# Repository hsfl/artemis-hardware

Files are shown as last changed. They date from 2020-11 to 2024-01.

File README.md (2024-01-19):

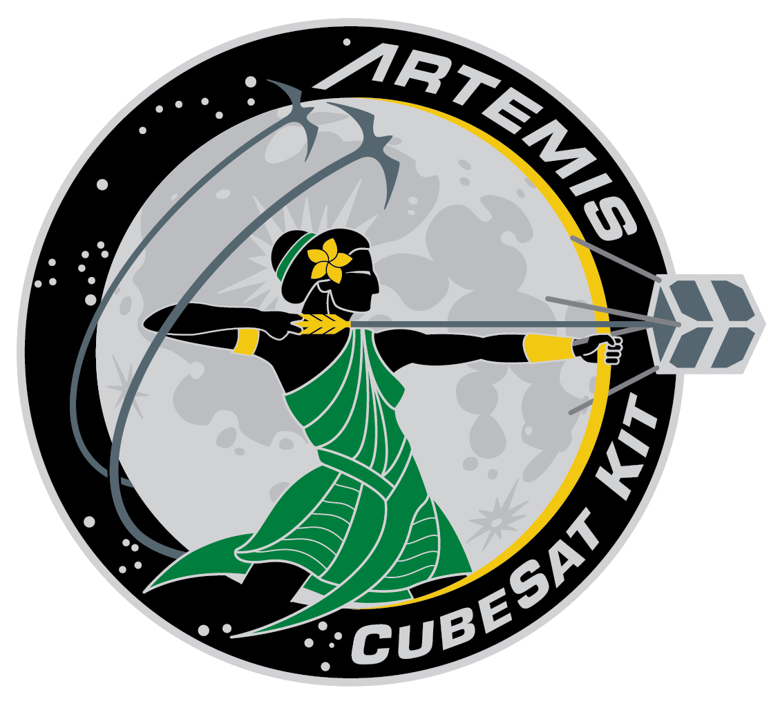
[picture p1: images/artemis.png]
Artemis
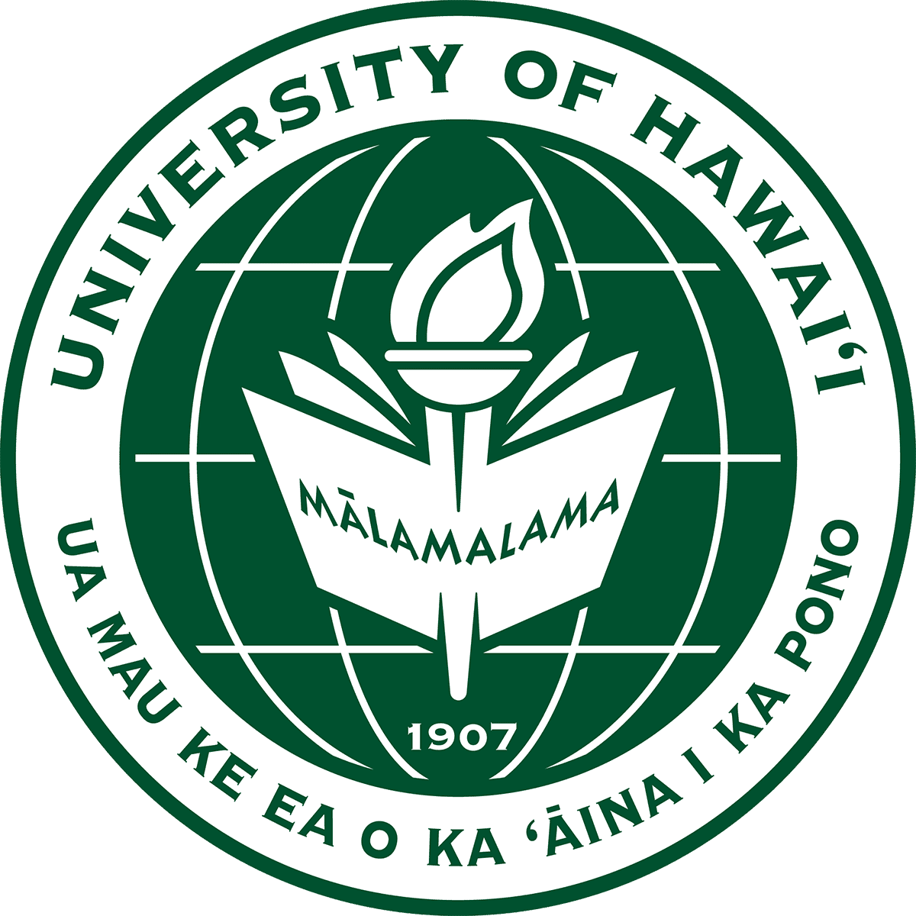
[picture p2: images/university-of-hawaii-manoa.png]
University of Hawaii Manoa
  <br>

# Artemis Cubesat Kit Hardware

This repository contains CAD models, Eagle designs, and thermal analysis for the Artemis Cubesat Kit V1.

For documentation and tutorials, visit our [project website](https://sites.google.com/hawaii.edu/artemiscubesatkit).

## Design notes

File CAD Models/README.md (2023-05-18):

Artemis University of Hawaii Manoa <br>

# Artemis Cubesat Kit Hardware

Within this folder are the solidworks files for the Artemis CubeSat.

Models were made using SolidWorks 2020, be sure to have SolidWorks 2020 or up to open the files.
If you do not have access to Solidworks, you can use OnShape to view the model as a zip file.

Due to file size limit, only the structure was uploaded.

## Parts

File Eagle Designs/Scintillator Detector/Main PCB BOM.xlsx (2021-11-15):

Part | Value | Device
C1 | 10uF | CAP0805
C2, C9 | 0.1uF | CAP0805
C3 | 10pF | CAP0805
C4 | 20nF | CAP0805
C5, C8 | 1uF | CAP0805
C6 | 22pF | CAP0805
C7 | 0.47uF | CAP0805
D1, D2 | RBR1VWM40ATR | RBR1VWM40ATR
J1, J2 | 503763-0591 | 503763-0591
L1 | 47uH | LQH32CN470K53L
L2 | BK2125LM252-T | BK2125LM252-T
R1 | 1k | RESISTOR0805-RES
R2 | 249 | RESISTOR0805-RES
R3, R4, R10, R13 | 10k | RESISTOR0805-RES
R5, R6 | 100k | RESISTOR0805-RES
R7, R9 | 0 | RESISTOR0805-RES
R8 | 24.9k | RESISTOR0805-RES
R11 | 226k | RESISTOR0805-RES
R12 | 45.3k | RESISTOR0805-RES
U1 | LT1807IS8PBF | LT1807IS8PBF
U2 | LT3461AES6TRMPBF | LT3461AES6TRMPBF
U3 | TMP36FSZ | TMP36FSZ

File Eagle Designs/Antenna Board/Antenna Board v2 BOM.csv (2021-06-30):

Part | Value | Device | Package | Description | AUTOMOTIVE | BUILT_BY | CENTROID_NOT_SPECIFIED | CONN_GENDER | CONN_ORIENTATION | CONTACT_MATERIAL | COPYRIGHT | CURRENT_RATING | DATASHEET | DEVICE_CLASS_L1 | DEVICE_CLASS_L2 | DEVICE_CLASS_L3 | DIGIKEY_DESCRIPTION | DIGIKEY_PART_NUMBER | FOOTPRINT_URL | FOOTPRINT_VARIANT_NAME_0 | HEIGHT | LEAD_FREE | MANUFACTURER_PART_NUMBER | MF | MFG_PACKAGE_IDENT | MFG_PACKAGE_IDENT_DATE | MFG_PACKAGE_IDENT_REV | MOUSER_PART_NUMBER | MPN | NUMBER_OF_CONTACTS | NUMBER_OF_ROWS | PACKAGE | PITCH | PREFIX | ROHS | SOURCELIBRARY | TEMPERATURE_RANGE_HIGH | TEMPERATURE_RANGE_LOW | VENDOR | VERIFICATION_VERSION | VOLTAGE_RATING
J1 | 503763-0591 | 503763-0591 | CONN_5037630591_MOL |  |  | EMA_Cory |  |  |  |  | Copyright (C) 2018 Accelerated Designs. All rights reserved |  | https://www.molex.com/pdm_docs/sd/5037630591_sd.pdf |  |  |  |  |  |  |  |  |  | 503763-0591 |  |  |  |  |  |  |  |  |  |  |  |  | Add_to_database_2020-12-14 |  |  | Molex Connector Corporation
J2 | MOLEX_503763-0491MOLEX_503763-0491_0_0 | MOLEX_503763-0491MOLEX_503763-0491_0_0 | MOLEX_503763-0491_0 | Wire-To-Board Connector, Pico-Lock 503763 Series, Surface Mount, Header, 4 Contacts, 1 mm | No |  | No | Male | Right Angle | Gold,Nickel |  | 1.5A | https://www.molex.com/webdocs/datasheets/pdf/en-us/5037630491_PCB_HEADERS.pdf | Connectors | Headers and Wire Housings | unset | CONN HEADER 1MM R/A 4CKT | WM10655CT-ND | https://www.molex.com/pdm_docs/sd/5037630491_sd.pdf | Recommended_Land_Pattern | 1.7mm | Yes |  | Molex | 503763-0491 | 0 | 0 | 538-503763-0491 | 503763-0491 | 4 | 1 | HDR4 | 1mm | J | Yes |  | +105°C | -40°C |  | 0.0.0.1 | 150V
J3 | MOLEX_503763-0491MOLEX_503763-0491_0_0 | MOLEX_503763-0491MOLEX_503763-0491_0_0 | MOLEX_503763-0491_0 | Wire-To-Board Connector, Pico-Lock 503763 Series, Surface Mount, Header, 4 Contacts, 1 mm | No |  | No | Male | Right Angle | Gold,Nickel |  | 1.5A | https://www.molex.com/webdocs/datasheets/pdf/en-us/5037630491_PCB_HEADERS.pdf | Connectors | Headers and Wire Housings | unset | CONN HEADER 1MM R/A 4CKT | WM10655CT-ND | https://www.molex.com/pdm_docs/sd/5037630491_sd.pdf | Recommended_Land_Pattern | 1.7mm | Yes |  | Molex | 503763-0491 | 0 | 0 | 538-503763-0491 | 503763-0491 | 4 | 1 | HDR4 | 1mm | J | Yes |  | +105°C | -40°C |  | 0.0.0.1 | 150V
J4 | MOLEX_503763-0291MOLEX_503763-0291_0_0 | MOLEX_503763-0291MOLEX_503763-0291_0_0 | MOLEX_503763-0291_0 | 2 Positions Header Connector 0.039 (1.00mm) Surface Mount, Right Angle Gold" |  |  | No |  |  |  |  |  | http://www.molex.com/pdm_docs/sd/5037630291_sd.pdf |  |  |  | CONN HEADER 1MM R/A 2CKT | WM10654CT-ND |  |  |  | yes |  | Molex |  |  |  | 538-503763-0291 | 503763-0291 |  |  | HDR02 |  | J | yes |  | +105°C | -40°C
J5 | 503763-0591 | 503763-0591 | CONN_5037630591_MOL |  |  | EMA_Cory |  |  |  |  | Copyright (C) 2018 Accelerated Designs. All rights reserved |  | https://www.molex.com/pdm_docs/sd/5037630591_sd.pdf |  |  |  |  |  |  |  |  |  | 503763-0591 |  |  |  |  |  |  |  |  |  |  |  |  | Add_to_database_2020-12-14 |  |  | Molex Connector Corporation
J6 | MOLEX_503763-0491MOLEX_503763-0491_0_0 | MOLEX_503763-0491MOLEX_503763-0491_0_0 | MOLEX_503763-0491_0 | Wire-To-Board Connector, Pico-Lock 503763 Series, Surface Mount, Header, 4 Contacts, 1 mm | No |  | No | Male | Right Angle | Gold,Nickel |  | 1.5A | https://www.molex.com/webdocs/datasheets/pdf/en-us/5037630491_PCB_HEADERS.pdf | Connectors | Headers and Wire Housings | unset | CONN HEADER 1MM R/A 4CKT | WM10655CT-ND | https://www.molex.com/pdm_docs/sd/5037630491_sd.pdf | Recommended_Land_Pattern | 1.7mm | Yes |  | Molex | 503763-0491 | 0 | 0 | 538-503763-0491 | 503763-0491 | 4 | 1 | HDR4 | 1mm | J | Yes |  | +105°C | -40°C |  | 0.0.0.1 | 150V
J7 | MOLEX_503763-0491MOLEX_503763-0491_0_0 | MOLEX_503763-0491MOLEX_503763-0491_0_0 | MOLEX_503763-0491_0 | Wire-To-Board Connector, Pico-Lock 503763 Series, Surface Mount, Header, 4 Contacts, 1 mm | No |  | No | Male | Right Angle | Gold,Nickel |  | 1.5A | https://www.molex.com/webdocs/datasheets/pdf/en-us/5037630491_PCB_HEADERS.pdf | Connectors | Headers and Wire Housings | unset | CONN HEADER 1MM R/A 4CKT | WM10655CT-ND | https://www.molex.com/pdm_docs/sd/5037630491_sd.pdf | Recommended_Land_Pattern | 1.7mm | Yes |  | Molex | 503763-0491 | 0 | 0 | 538-503763-0491 | 503763-0491 | 4 | 1 | HDR4 | 1mm | J | Yes |  | +105°C | -40°C |  | 0.0.0.1 | 150V
J8 | MOLEX_503763-0291MOLEX_503763-0291_0_0 | MOLEX_503763-0291MOLEX_503763-0291_0_0 | MOLEX_503763-0291_0 | 2 Positions Header Connector 0.039 (1.00mm) Surface Mount, Right Angle Gold" |  |  | No |  |  |  |  |  | http://www.molex.com/pdm_docs/sd/5037630291_sd.pdf |  |  |  | CONN HEADER 1MM R/A 2CKT | WM10654CT-ND |  |  |  | yes |  | Molex |  |  |  | 538-503763-0291 | 503763-0291 |  |  | HDR02 |  | J | yes |  | +105°C | -40°C
J9 | MOLEX_503763-0291MOLEX_503763-0291_0_0 | MOLEX_503763-0291MOLEX_503763-0291_0_0 | MOLEX_503763-0291_0 | 2 Positions Header Connector 0.039 (1.00mm) Surface Mount, Right Angle Gold" |  |  | No |  |  |  |  |  | http://www.molex.com/pdm_docs/sd/5037630291_sd.pdf |  |  |  | CONN HEADER 1MM R/A 2CKT | WM10654CT-ND |  |  |  | yes |  | Molex |  |  |  | 538-503763-0291 | 503763-0291 |  |  | HDR02 |  | J | yes |  | +105°C | -40°C
J10 | U.FL-R-SMT-1(01) | U.FL-R-SMT-1(01) | CONN_-SMT-1(01) |  |  | EMA_Matt |  |  |  |  | Copyright (C) 2018 Accelerated Designs. All rights reserved |  |  |  |  |  |  |  |  |  |  |  | U.FL-R-SMT-1(01) |  |  |  |  |  |  |  |  |  |  |  |  | Hirose_12_20_2019 |  |  | Hirose
J11 | U.FL-R-SMT-1(01) | U.FL-R-SMT-1(01) | CONN_-SMT-1(01) |  |  | EMA_Matt |  |  |  |  | Copyright (C) 2018 Accelerated Designs. All rights reserved |  |  |  |  |  |  |  |  |  |  |  | U.FL-R-SMT-1(01) |  |  |  |  |  |  |  |  |  |  |  |  | Hirose_12_20_2019 |  |  | Hirose
J12 | U.FL-R-SMT-1(01) | U.FL-R-SMT-1(01) | CONN_-SMT-1(01) |  |  | EMA_Matt |  |  |  |  | Copyright (C) 2018 Accelerated Designs. All rights reserved |  |  |  |  |  |  |  |  |  |  |  | U.FL-R-SMT-1(01) |  |  |  |  |  |  |  |  |  |  |  |  | Hirose_12_20_2019 |  |  | Hirose
U$2 | ANTENNA_PAD | ANTENNA_PAD | ANTENNA_PAD
U$3 | BURNWIRE | BURNWIRE | BURNWIRE

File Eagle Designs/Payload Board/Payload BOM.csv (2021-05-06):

Part | Value | Device | Package | Description | ARROW_PART_NUMBER | ARROW_PRICE-STOCK | AUTOMOTIVE | AVAILABILITY | BUILT_BY | CENTROID_NOT_SPECIFIED | CONN_GENDER | CONN_ORIENTATION | CONTACT_MATERIAL | COPYRIGHT | CURRENT_RATING | DATASHEET | DESCRIPTION | DEVICE_CLASS_L1 | DEVICE_CLASS_L2 | DEVICE_CLASS_L3 | DIGIKEY_DESCRIPTION | DIGIKEY_PART_NUMBER | FOOTPRINT_URL | FOOTPRINT_VARIANT_NAME_0 | HEIGHT | LEAD_FREE | MANUFACTURER_NAME | MANUFACTURER_PART_NUMBER | MF | MFG_PACKAGE_IDENT | MFG_PACKAGE_IDENT_DATE | MFG_PACKAGE_IDENT_REV | MOUSER_PART_NUMBER | MOUSER_PRICE-STOCK | MP | MPN | NUMBER_OF_CONTACTS | NUMBER_OF_ROWS | OC_FARNELL | OC_NEWARK | PACKAGE | PITCH | PREFIX | PRICE | PURCHASE-URL | ROHS | SOURCELIBRARY | TEMPERATURE_RANGE_HIGH | TEMPERATURE_RANGE_LOW | VENDOR | VERIFICATION_VERSION | VOLTAGE_RATING
C1 | 22uF | CAP0805 | 0805 | Capacitor
C2 | 22uF | CAP0805 | 0805 | Capacitor
C3 | 0.1uF | CAP0805 | 0805 | Capacitor
C4 | 1uF | CAP0805 | 0805 | Capacitor
C5 | 0.47uF | CAP0805 | 0805 | Capacitor
C6 | 0.1uF | CAP0805 | 0805 | Capacitor
C7 | 100pF | CAP0805 | 0805 | Capacitor
C8 | 4.7uF | CAP0805 | 0805 | Capacitor
C9 | 1uF | CAP0805 | 0805 | Capacitor
C10 | 0.1uF | CAP0805 | 0805 | Capacitor
C11 | 4.7nF | CAP0805 | 0805 | Capacitor
C12 | 10uF | CAP0805 | 0805 | Capacitor
C13 | 4.7uF | CAP0805 | 0805 | Capacitor
C14 | 10uF | CAP0805 | 0805 | Capacitor
C15 | 4.7uF | CAP0805 | 0805 | Capacitor
C16 | 4.7uF | CAP0805 | 0805 | Capacitor
C17 | 10uF | CAP0805 | 0805 | Capacitor
C18 | 0.1uF | CAP0805 | 0805 | Capacitor
C19 | 10uF | CAP0805 | 0805 | Capacitor
C20 | 0.1uF | CAP0805 | 0805 | Capacitor
C52 | 0.1uF | CAP0805 | 0805 | Capacitor
C53 | 1uF | CAP0805 | 0805 | Capacitor
C54 | 10pF | CAP0805 | 0805 | Capacitor
C55 | 47uF | CAP1210 | 1210 | Capacitor
C56 | 4.7uF | CAP0805 | 0805 | Capacitor
C57 | 0.1uF | CAP0805 | 0805 | Capacitor
C62 | 0.1uF | CAP0805 | 0805 | Capacitor
C74 | 33uF | CAP1206 | 1206 | Capacitor
C75 | 33uF | CAP1206 | 1206 | Capacitor
C76 | 33uF | CAP1206 | 1206 | Capacitor
C77 | 33uF | CAP1206 | 1206 | Capacitor
C78 | 33uF | CAP1206 | 1206 | Capacitor
C79 | 33uF | CAP1206 | 1206 | Capacitor
C80 | 33uF | CAP1206 | 1206 | Capacitor
C81 | 33uF | CAP1206 | 1206 | Capacitor
D4 |  | DIODE_SOD-123FL | SOD-123FL | Diode
H1 | PC104_WCONN | PC104_WCONN | PC104_WCONN
J1 | 503763-0591 | 503763-0591 | CONN_5037630591_MOL |  |  |  |  |  | EMA_Cory |  |  |  |  | Copyright (C) 2018 Accelerated Designs. All rights reserved |  | https://www.molex.com/pdm_docs/sd/5037630591_sd.pdf |  |  |  |  |  |  |  |  |  |  |  | 503763-0591 |  |  |  |  |  |  |  |  |  |  |  |  |  |  |  |  |  |  | Add_to_database_2020-12-14 |  |  | Molex Connector Corporation
J2 | 503763-0591 | 503763-0591 | CONN_5037630591_MOL |  |  |  |  |  | EMA_Cory |  |  |  |  | Copyright (C) 2018 Accelerated Designs. All rights reserved |  | https://www.molex.com/pdm_docs/sd/5037630591_sd.pdf |  |  |  |  |  |  |  |  |  |  |  | 503763-0591 |  |  |  |  |  |  |  |  |  |  |  |  |  |  |  |  |  |  | Add_to_database_2020-12-14 |  |  | Molex Connector Corporation
J3 | MOLEX_503763-0491MOLEX_503763-0491_0_0 | MOLEX_503763-0491MOLEX_503763-0491_0_0 | MOLEX_503763-0491_0 | Wire-To-Board Connector, Pico-Lock 503763 Series, Surface Mount, Header, 4 Contacts, 1 mm |  |  | No |  |  | No | Male | Right Angle | Gold,Nickel |  | 1.5A | https://www.molex.com/webdocs/datasheets/pdf/en-us/5037630491_PCB_HEADERS.pdf |  | Connectors | Headers and Wire Housings | unset | CONN HEADER 1MM R/A 4CKT | WM10655CT-ND | https://www.molex.com/pdm_docs/sd/5037630491_sd.pdf | Recommended_Land_Pattern | 1.7mm | Yes |  |  | Molex | 503763-0491 | 0 | 0 | 538-503763-0491 |  |  | 503763-0491 | 4 | 1 |  |  | HDR4 | 1mm | J |  |  | Yes |  | +105°C | -40°C |  | 0.0.0.1 | 150V
J4 | 503763-0691 | 503763-0691 | CONN_503763-0691_MOL |  |  |  |  |  | EMA_Cory |  |  |  |  | Copyright (C) 2018 Accelerated Designs. All rights reserved |  | https://www.digikey.com/products/en?keywords=503763-0691 |  |  |  |  |  |  |  |  |  |  |  | 503763-0691 |  |  |  |  |  |  |  |  |  |  |  |  |  |  |  |  |  |  | Molex_2020-01-22 |  |  | Molex Connector Corporation
J5 | MOLEX_503763-0291MOLEX_503763-0291_0_0 | MOLEX_503763-0291MOLEX_503763-0291_0_0 | MOLEX_503763-0291_0 | 2 Positions Header Connector 0.039 (1.00mm) Surface Mount, Right Angle Gold" |  |  |  |  |  | No |  |  |  |  |  | http://www.molex.com/pdm_docs/sd/5037630291_sd.pdf |  |  |  |  | CONN HEADER 1MM R/A 2CKT | WM10654CT-ND |  |  |  | yes |  |  | Molex |  |  |  | 538-503763-0291 |  |  | 503763-0291 |  |  |  |  | HDR02 |  | J |  |  | yes |  | +105°C | -40°C
J6 | 503763-0691 | 503763-0691 | CONN_503763-0691_MOL |  |  |  |  |  | EMA_Cory |  |  |  |  | Copyright (C) 2018 Accelerated Designs. All rights reserved |  | https://www.digikey.com/products/en?keywords=503763-0691 |  |  |  |  |  |  |  |  |  |  |  | 503763-0691 |  |  |  |  |  |  |  |  |  |  |  |  |  |  |  |  |  |  | Molex_2020-01-22 |  |  | Molex Connector Corporation
J7 | 503763-0691 | 503763-0691 | CONN_503763-0691_MOL |  |  |  |  |  | EMA_Cory |  |  |  |  | Copyright (C) 2018 Accelerated Designs. All rights reserved |  | https://www.digikey.com/products/en?keywords=503763-0691 |  |  |  |  |  |  |  |  |  |  |  | 503763-0691 |  |  |  |  |  |  |  |  |  |  |  |  |  |  |  |  |  |  | Molex_2020-01-22 |  |  | Molex Connector Corporation
J8 | MOLEX_503763-0491MOLEX_503763-0491_0_0 | MOLEX_503763-0491MOLEX_503763-0491_0_0 | MOLEX_503763-0491_0 | Wire-To-Board Connector, Pico-Lock 503763 Series, Surface Mount, Header, 4 Contacts, 1 mm |  |  | No |  |  | No | Male | Right Angle | Gold,Nickel |  | 1.5A | https://www.molex.com/webdocs/datasheets/pdf/en-us/5037630491_PCB_HEADERS.pdf |  | Connectors | Headers and Wire Housings | unset | CONN HEADER 1MM R/A 4CKT | WM10655CT-ND | https://www.molex.com/pdm_docs/sd/5037630491_sd.pdf | Recommended_Land_Pattern | 1.7mm | Yes |  |  | Molex | 503763-0491 | 0 | 0 | 538-503763-0491 |  |  | 503763-0491 | 4 | 1 |  |  | HDR4 | 1mm | J |  |  | Yes |  | +105°C | -40°C |  | 0.0.0.1 | 150V
J9 | MOLEX_503763-0491MOLEX_503763-0491_0_0 | MOLEX_503763-0491MOLEX_503763-0491_0_0 | MOLEX_503763-0491_0 | Wire-To-Board Connector, Pico-Lock 503763 Series, Surface Mount, Header, 4 Contacts, 1 mm |  |  | No |  |  | No | Male | Right Angle | Gold,Nickel |  | 1.5A | https://www.molex.com/webdocs/datasheets/pdf/en-us/5037630491_PCB_HEADERS.pdf |  | Connectors | Headers and Wire Housings | unset | CONN HEADER 1MM R/A 4CKT | WM10655CT-ND | https://www.molex.com/pdm_docs/sd/5037630491_sd.pdf | Recommended_Land_Pattern | 1.7mm | Yes |  |  | Molex | 503763-0491 | 0 | 0 | 538-503763-0491 |  |  | 503763-0491 | 4 | 1 |  |  | HDR4 | 1mm | J |  |  | Yes |  | +105°C | -40°C |  | 0.0.0.1 | 150V
L1 | 6uH | 7443551600 | 7443551600
L6 | 10uH | XFL4020-222MEC | XFL4030472MEB | COILCRAFT - XFL4020-222MEC - INDUCTOR, 2.2UH, 8A, 20%, PWR, 38MHZ | XFL4020-222MEC |  |  |  |  |  |  |  |  |  |  |  | COILCRAFT - XFL4020-222MEC - INDUCTOR, 2.2UH, 8A, 20%, PWR, 38MHZ |  |  |  |  |  |  |  | 3mm |  | COILCRAFT | XFL4020-222MEC |  |  |  |  | 994-XFL4020-222MEC | https://www.mouser.co.uk/ProductDetail/Coilcraft/XFL4020-222MEC?qs=zCSbvcPd3pbe5jEAG1ZkEA%3D%3D
M1 | BSZ100N06LS3 | BSZ100N06LS3 | BSZ100N06LS3
M2 | BSZ100N06LS3 | BSZ100N06LS3 | BSZ100N06LS3
M3 | BSZ033NE2LS5 | BSZ100N06LS3 | BSZ100N06LS3
M4 | BSZ033NE2LS5 | BSZ100N06LS3 | BSZ100N06LS3
R1 | 1M | RESISTOR0805-RES | 0805 | Resistor
R2 | 390K | RESISTOR0805-RES | 0805 | Resistor
R3 | 180K | RESISTOR0805-RES | 0805 | Resistor
R4 | 27K | RESISTOR0805-RES | 0805 | Resistor
R5 | 100K | RESISTOR0805-RES | 0805 | Resistor
R6 | 100K | RESISTOR0805-RES | 0805 | Resistor
R7 | 4m | RESISTOR0805-RES | 0805 | Resistor
R8 | 15m | RESISTOR0805-RES | 0805 | Resistor
R9 | 130K | RESISTOR0805-RES | 0805 | Resistor
R10 | 10K | RESISTOR0805-RES | 0805 | Resistor
R11 | 330m | RESISTOR0805-RES | 0805 | Resistor
R12 | 330m | RESISTOR0805-RES | 0805 | Resistor
R13 | 3.3k | RESISTOR0805-RES | 0805 | Resistor
R14 | 330m | RESISTOR0805-RES | 0805 | Resistor
R15 | 330m | RESISTOR0805-RES | 0805 | Resistor
R16 | 3.3k | RESISTOR0805-RES | 0805 | Resistor
R32 | 10K | RESISTOR0805-RES | 0805 | Resistor
R37 | 10K | RESISTOR0805-RES | 0805 | Resistor
R38 | 10K | RESISTOR0805-RES | 0805 | Resistor
R46 | 510K | RESISTOR0805-RES | 0805 | Resistor
R47 | 270K | RESISTOR0805-RES | 0805 | Resistor
R51 | 40.2K | RESISTOR0805-RES | 0805 | Resistor
R52 | 100K | RESISTOR0805-RES | 0805 | Resistor
R53 | 1.0M | RESISTOR0805-RES | 0805 | Resistor
R54 | 69.8K | RESISTOR0805-RES | 0805 | Resistor
U$2 | LT8309EFE | LT8309EFE | LT8309EFE
U1 | DRV8847PWPR | DRV8847PWPR | SOP65P640X120-17N | None Check prices |  |  |  | Warning |  |  |  |  |  |  |  |  | 18-V, 2-A dual H-bridge motor driver with current regulation & independent half-bridge control 16-HTSSOP -40 to 125 |  |  |  |  |  |  |  |  |  |  |  | Texas Instruments |  |  |  |  |  | DRV8847PWPR |  |  |  |  |  | HTSSOP-16 Texas Instruments |  |  | None | https://pricing.snapeda.com/search/part/DRV8847PWPR/?ref=eda
U2 | DRV8847PWPR | DRV8847PWPR | SOP65P640X120-17N | None Check prices |  |  |  | Warning |  |  |  |  |  |  |  |  | 18-V, 2-A dual H-bridge motor driver with current regulation & independent half-bridge control 16-HTSSOP -40 to 125 |  |  |  |  |  |  |  |  |  |  |  | Texas Instruments |  |  |  |  |  | DRV8847PWPR |  |  |  |  |  | HTSSOP-16 Texas Instruments |  |  | None | https://pricing.snapeda.com/search/part/DRV8847PWPR/?ref=eda
U5 | LT8609A | LT8609A | MSOP-10_MSE
U11 | ADT7311 | ADT7311 | SOIC-8 | The ADT7311 is a high accuracy digital temperature sensor
X1 | C25582-40G-M36-0A | C25582-40G-M36-0A | ADAFRUIT_C25582-40G-M36-0A_0
X2 | SSW-120-02-G-D | SSW-120-02-G-D | SSW-120-02-G-D | THROUGH-HOLE .025 SQ POST SOCKET" |  |  |  |  |  |  |  |  |  |  |  |  |  |  |  |  |  |  |  |  |  |  |  |  | Samtec Inc. |  |  |  |  |  |  | SSW-120-02-G-D |  |  | unknown | 11P9639

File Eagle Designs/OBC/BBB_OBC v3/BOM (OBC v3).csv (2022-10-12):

Part | Value | Device | Package | Description | AUTOMOTIVE | AVAILABILITY | BUILT_BY | CENTROID_NOT_SPECIFIED | CIIVA_IDS | COMPONENT_LINK_1_DESCRIPTION | COMPONENT_LINK_1_URL | COMPONENT_LINK_3_DESCRIPTION | COMPONENT_LINK_3_URL | CONN_GENDER | CONN_ORIENTATION | CONTACT_MATERIAL | COPYRIGHT | CURRENT_RATING | DATASHEET | DESCRIPTION | DEVICE_CLASS_L1 | DEVICE_CLASS_L2 | DEVICE_CLASS_L3 | DIGIKEY_DESCRIPTION | DIGIKEY_PART_NUMBER | FOOTPRINT_URL | FOOTPRINT_VARIANT_NAME_0 | FOOTPRINT_VARIANT_NAME_1 | FOOTPRINT_VARIANT_NAME_2 | HEIGHT | IMPORTED | IMPORTED_FROM | IMPORT_TS | LEAD_FREE | MANUFACTURER_PART_NUMBER | MF | MFG_PACKAGE_IDENT | MFG_PACKAGE_IDENT_DATE | MFG_PACKAGE_IDENT_REV | MFR_NAME | MOUNTING_TECHNOLOGY | MOUSER_PART_NUMBER | MP | MPN | NUMBER_OF_CONTACTS | NUMBER_OF_ROWS | OC_FARNELL | OC_NEWARK | PACKAGE | PACKAGE_DESCRIPTION | PACKAGE_VERSION | PITCH | POPULARITY | PREFIX | PRICE | RELEASE_DATE | ROHS | SOURCELIBRARY | TEMPERATURE_RANGE_HIGH
3V3_BUS |  | 1,6/0,9 | 1,6/0,9 | THROUGH-HOLE PAD |  |  |  |  |  |  |  |  |  |  |  |  |  |  |  |  |  |  |  |  |  |  |  |  |  |  |  |  |  |  |  |  |  |  |  |  |  |  |  |  |  |  |  |  |  |  |  |  | 7
C1 | .1uF | CAP0805 | 805 | Capacitor
C2 | 1uF | CAP0805 | 805 | Capacitor
C3 | 1uF | CAP0805 | 805 | Capacitor
D1 |  | LEDCHIP-LED0603 | CHIP-LED0603 | LED |  |  |  |  |  |  |  |  |  |  |  |  |  |  |  |  |  |  |  |  |  |  |  |  |  |  |  |  |  |  |  |  |  |  |  |  |  |  |  |  |  |  |  |  |  |  |  |  | 26
GND | GND | 1,6/0,9 | 1,6/0,9 | THROUGH-HOLE PAD |  |  |  |  |  |  |  |  |  |  |  |  |  |  |  |  |  |  |  |  |  |  |  |  |  |  |  |  |  |  |  |  |  |  |  |  |  |  |  |  |  |  |  |  |  |  |  |  | 7
GPS_BOOTSEL |  | 1,6/0,9 | 1,6/0,9 | THROUGH-HOLE PAD |  |  |  |  |  |  |  |  |  |  |  |  |  |  |  |  |  |  |  |  |  |  |  |  |  |  |  |  |  |  |  |  |  |  |  |  |  |  |  |  |  |  |  |  |  |  |  |  | 7
H1 | SSQ-126-22-G-D | SSQ-126-22-G-D |  | Large PC104 receptacle |  |  |  |  |  |  |  |  |  |  |  |  |  |  | https://www.mouser.com/datasheet/2/527/ssq_th-1370157.pdf
H2 | SSQ-126-22-G-D | SSQ-126-22-G-D |  | Large PC104 receptacle |  |  |  |  |  |  |  |  |  |  |  |  |  |  | https://www.mouser.com/datasheet/2/527/ssq_th-1370157.pdf
J1 | MOLEX_503763-0491MOLEX_503763-0491_0_0 | MOLEX_503763-0491MOLEX_503763-0491_0_0 | MOLEX_503763-0491_0 | Wire-To-Board Connector, Pico-Lock 503763 Series, Surface Mount, Header, 4 Contacts, 1 mm | No |  |  | No |  |  |  |  |  | Male | Right Angle | Gold,Nickel |  | 1.5A | https://www.molex.com/webdocs/datasheets/pdf/en-us/5037630491_PCB_HEADERS.pdf |  | Connectors | Headers and Wire Housings | unset | CONN HEADER 1MM R/A 4CKT | WM10655CT-ND | https://www.molex.com/pdm_docs/sd/5037630491_sd.pdf | Recommended_Land_Pattern |  |  | 1.7mm |  |  |  | Yes |  | Molex | 503763-0491 | 0 | 0 |  |  | 538-503763-0491 |  | 503763-0491 | 4 | 1 |  |  | HDR4 |  |  | 1mm |  | J |  |  | Yes |  | +105°C
J2 | MOLEX_503763-0491MOLEX_503763-0491_0_0 | MOLEX_503763-0491MOLEX_503763-0491_0_0 | MOLEX_503763-0491_0 | Wire-To-Board Connector, Pico-Lock 503763 Series, Surface Mount, Header, 4 Contacts, 1 mm | No |  |  | No |  |  |  |  |  | Male | Right Angle | Gold,Nickel |  | 1.5A | https://www.molex.com/webdocs/datasheets/pdf/en-us/5037630491_PCB_HEADERS.pdf |  | Connectors | Headers and Wire Housings | unset | CONN HEADER 1MM R/A 4CKT | WM10655CT-ND | https://www.molex.com/pdm_docs/sd/5037630491_sd.pdf | Recommended_Land_Pattern |  |  | 1.7mm |  |  |  | Yes |  | Molex | 503763-0491 | 0 | 0 |  |  | 538-503763-0491 |  | 503763-0491 | 4 | 1 |  |  | HDR4 |  |  | 1mm |  | J |  |  | Yes |  | +105°C
J6 | MOLEX_503763-0491MOLEX_503763-0491_0_0 | MOLEX_503763-0491MOLEX_503763-0491_0_0 | MOLEX_503763-0491_0 | Wire-To-Board Connector, Pico-Lock 503763 Series, Surface Mount, Header, 4 Contacts, 1 mm | No |  |  | No |  |  |  |  |  | Male | Right Angle | Gold,Nickel |  | 1.5A | https://www.molex.com/webdocs/datasheets/pdf/en-us/5037630491_PCB_HEADERS.pdf |  | Connectors | Headers and Wire Housings | unset | CONN HEADER 1MM R/A 4CKT | WM10655CT-ND | https://www.molex.com/pdm_docs/sd/5037630491_sd.pdf | Recommended_Land_Pattern |  |  | 1.7mm |  |  |  | Yes |  | Molex | 503763-0491 | 0 | 0 |  |  | 538-503763-0491 |  | 503763-0491 | 4 | 1 |  |  | HDR4 |  |  | 1mm |  | J |  |  | Yes |  | +105°C
J9 | U.FL-R-SMT-1(01) | U.FL-R-SMT-1(01) | CONN_-SMT-1(01) |  |  |  | EMA_Matt |  |  |  |  |  |  |  |  |  | Copyright (C) 2018 Accelerated Designs. All rights reserved |  |  |  |  |  |  |  |  |  |  |  |  |  |  |  |  |  | U.FL-R-SMT-1(01) |  |  |  |  |  |  |  |  |  |  |  |  |  |  |  |  |  |  |  |  |  |  | Hirose_12_20_2019
J10 | 503763-0591 | 503763-0591 | CONN_5037630591_MOL |  |  |  | EMA_Cory |  |  |  |  |  |  |  |  |  | Copyright (C) 2018 Accelerated Designs. All rights reserved |  | https://www.molex.com/pdm_docs/sd/5037630591_sd.pdf |  |  |  |  |  |  |  |  |  |  |  |  |  |  |  | 503763-0591 |  |  |  |  |  |  |  |  |  |  |  |  |  |  |  |  |  |  |  |  |  |  | Add_to_database_2020-12-14
J11 | 503763-0591 | 503763-0591 | CONN_5037630591_MOL |  |  |  | EMA_Cory |  |  |  |  |  |  |  |  |  | Copyright (C) 2018 Accelerated Designs. All rights reserved |  | https://www.molex.com/pdm_docs/sd/5037630591_sd.pdf |  |  |  |  |  |  |  |  |  |  |  |  |  |  |  | 503763-0591 |  |  |  |  |  |  |  |  |  |  |  |  |  |  |  |  |  |  |  |  |  |  | Add_to_database_2020-12-14
J12 | 503763-0691 | 503763-0691 | CONN_503763-0691_MOL |  |  |  | EMA_Cory |  |  |  |  |  |  |  |  |  | Copyright (C) 2018 Accelerated Designs. All rights reserved |  | https://www.digikey.com/products/en?keywords=503763-0691 |  |  |  |  |  |  |  |  |  |  |  |  |  |  |  | 503763-0691 |  |  |  |  |  |  |  |  |  |  |  |  |  |  |  |  |  |  |  |  |  |  | Molex_2020-01-22
J13 | MOLEX_503763-0291MOLEX_503763-0291_0_0 | MOLEX_503763-0291MOLEX_503763-0291_0_0 | MOLEX_503763-0291_0 | 2 Positions Header Connector 0.039 (1.00mm) Surface Mount, Right Angle Gold" |  |  |  | No |  |  |  |  |  |  |  |  |  |  | http://www.molex.com/pdm_docs/sd/5037630291_sd.pdf |  |  |  |  | CONN HEADER 1MM R/A 2CKT | WM10654CT-ND |  |  |  |  |  |  |  |  | yes |  | Molex |  |  |  |  |  | 538-503763-0291 |  | 503763-0291 |  |  |  |  | HDR02 |  |  |  |  | J |  |  | yes |  | +105°C
J16 | U.FL-R-SMT-1(01) | U.FL-R-SMT-1(01) | CONN_-SMT-1(01) |  |  |  | EMA_Matt |  |  |  |  |  |  |  |  |  | Copyright (C) 2018 Accelerated Designs. All rights reserved |  |  |  |  |  |  |  |  |  |  |  |  |  |  |  |  |  | U.FL-R-SMT-1(01) |  |  |  |  |  |  |  |  |  |  |  |  |  |  |  |  |  |  |  |  |  |  | Hirose_12_20_2019
JP4 | FR20206VBNN | Receptacle | 1X06_ROUND_70 | PIN HEADER |  |  |  |  |  |  |  |  |  |  |  |  |  |  | https://media.metz-connect.com/files/171/Data_sheet_FR202XXVBNN.PDF
JP5 | MOLEX_503763-0291MOLEX_503763-0291_0_0 | MOLEX_503763-0291MOLEX_503763-0291_0_0 | MOLEX_503763-0291_0 | 2 Positions Header Connector 0.039 (1.00mm) Surface Mount, Right Angle Gold" |  |  |  | No |  |  |  |  |  |  |  |  |  |  | http://www.molex.com/pdm_docs/sd/5037630291_sd.pdf |  |  |  |  | CONN HEADER 1MM R/A 2CKT | WM10654CT-ND |  |  |  |  |  |  |  |  | yes |  | Molex |  |  |  |  |  | 538-503763-0291 |  | 503763-0291 |  |  |  |  | HDR02 |  |  |  |  | J |  |  | yes |  | +105°C
JP6 | 503763-0691 | 503763-0691 | CONN_503763-0691_MOL |  |  |  | EMA_Cory |  |  |  |  |  |  |  |  |  | Copyright (C) 2018 Accelerated Designs. All rights reserved |  | https://www.digikey.com/products/en?keywords=503763-0691 |  |  |  |  |  |  |  |  |  |  |  |  |  |  |  | 503763-0691 |  |  |  |  |  |  |  |  |  |  |  |  |  |  |  |  |  |  |  |  |  |  | Molex_2020-01-22
JP7 | 503763-0691 | 503763-0691 | CONN_503763-0691_MOL |  |  |  | EMA_Cory |  |  |  |  |  |  |  |  |  | Copyright (C) 2018 Accelerated Designs. All rights reserved |  | https://www.digikey.com/products/en?keywords=503763-0691 |  |  |  |  |  |  |  |  |  |  |  |  |  |  |  | 503763-0691 |  |  |  |  |  |  |  |  |  |  |  |  |  |  |  |  |  |  |  |  |  |  | Molex_2020-01-22
P8 | SSW-123-02-G-D | SSW-123-02-G-D | SSW-123-02-G-D | THROUGH-HOLE .025 SQ POST SOCKET" |  |  |  |  |  |  |  |  |  |  |  |  |  |  |  |  |  |  |  |  |  |  |  |  |  |  |  |  |  |  |  | Samtec Inc. |  |  |  |  |  |  |  | SSW-123-02-G-D |  |  | unknown | 11P9690
P9 | SSW-123-02-G-D | SSW-123-02-G-D | SSW-123-02-G-D | THROUGH-HOLE .025 SQ POST SOCKET" |  |  |  |  |  |  |  |  |  |  |  |  |  |  |  |  |  |  |  |  |  |  |  |  |  |  |  |  |  |  |  | Samtec Inc. |  |  |  |  |  |  |  | SSW-123-02-G-D |  |  | unknown | 11P9690
R1 | 27k | RESISTOR0805-RES | 805 | Resistor
R2 | 10k | RESISTOR0805-RES | 805 | Resistor
R66 | 1M | RESISTOR0805-RES | 805 | Resistor
U1 | TMP36FSZR_8_ADI-L | TMP36FSZR_8_ADI-L | R_8_ADI-L |  |  |  |  |  |  |  |  |  |  |  |  |  | Copyright (C) 2021 Ultra Librarian. All rights reserved. |  |  |  |  |  |  |  |  |  |  |  |  |  |  |  |  |  | TMP36FSZ |  |  |  |  | Analog Devices Inc
U2 | LTC1477CS8LINEAR_TECHNOLOGY_LTC1477CS8_0_2 | LTC1477CS8LINEAR_TECHNOLOGY_LTC1477CS8_0_2 | LINEAR_TECHNOLOGY_LTC1477CS8_2 | LT-LTC1477-S8-8 |  |  |  |  | 1432281 | Manufacturer URL | http://www.linear.com/ | Package Specification | http://cds.linear.com/docs/en/packaging/05081610_G_SO8.pdf |  |  |  |  |  | http://cds.linear.com/docs/en/datasheet/lt1477.pdf |  |  |  |  |  |  |  | Level C | Level B | Level A |  | yes | vault | 1521843574 |  |  | Linear Technology |  |  |  |  | Surface Mount |  |  | LTC1477CS8 |  |  |  |  | S8-8 | 8-Pin Plastic Small Outline (Narrow .150 Inch), Body 4.9 x 3.9 mm, Pitch 1.27 mm | Rev. G, 03/2012 |  |  | U |  | 1377817843 | No
U5 | RFM69HCW | RFM69HCW | RFM69HCW | Rfm69hcw Wireless Transceiver 91 Check prices |  | No availability data |  |  |  |  |  |  |  |  |  |  |  |  |  | General ISM < 1GHz Transceiver Module 915MHz Surface Mount |  |  |  |  |  |  |  |  |  |  |  |  |  |  |  | HOPERF |  |  |  |  |  |  | RFM69HCW-315S2 |  |  |  |  |  | Module SparkFun Electronics |  |  |  |  |  | None
U6 | ORION_A38LORION_A38L | ORION_A38LORION_A38L | ORION_A38L
X1 | C25582-40G-M36-0A | C25582-40G-M36-0A | ADAFRUIT_C25582-40G-M36-0A_0
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

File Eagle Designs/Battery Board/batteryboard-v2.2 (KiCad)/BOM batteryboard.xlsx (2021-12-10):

Id | Designator | Package | Quantity | Designation | Supplier and ref | Column1 | _1
1 | R6 | R_0805_2012Metric | 1 | 10k
2 | R5 | R_0805_2012Metric | 1 | 45.3k
3 | J2,J4,J6,J5,J3,J1 | KEYSTONE-1042 | 6 | KEYSTONE-1042
4 | Ref** | battery_version | 1 | Val**
5 | H3,H4,H2,H1 | MountingHole_3.2mm_M3_DIN965_PadMOD | 4 | MountingHole_Pad
6 | Ref** | pycubed_logo | 1 | Val**
7 | REF**,REF**,REF**,REF**,REF**,REF** | Fiducial_0.75mm_Mask1.5mm | 6 | Fiducial_0.75mm_Mask1.5mm
8 | TH1 | R_Axial_DIN0204_L3.6mm_D1.6mm_P5.08mm_Vertical | 1 | Thermistor
9 | J12 | PinHeader_1x01_P1.00mm_Vertical | 1 | Screw_Terminal_01x01
10 | TP4,TP3,TP2,TP1 | TestPoint_Loop_D1.80mm_Drill1.0mm_Beaded | 4 | TestPoint
11 | C3,C4,C2,C1,C5 | C_0603_1608Metric | 4 | 0.1uF
12 | R4 | R_0603_1608Metric | 1 | 1K
13 | R2,R1 | R_0603_1608Metric | 2 | 330
14 | R3 | R_2512_6332Metric | 1 | 0.01
15 | Q2,Q1 | SOIC-8_3.9x4.9mm_P1.27mm | 2 | IRF7458
16 | U1 | SOT95P280X130-6N | 1 | R5460N233AF
17 | J7,J8,J10,J11 | Molex_Pico-Lock_503763-0291_1x02-1MP_P1.00m_Horizontal | 4 | Conn_01x02_Female
18 | J9 | Molex_Pico-Lock_503763-0491_1x04-1MP_P1.00mm_Horizontal | 1 | Conn_01x04_Female
19 | U2 | TMP36FSZ-REEL | 1 | TMP36FSZ-REEL

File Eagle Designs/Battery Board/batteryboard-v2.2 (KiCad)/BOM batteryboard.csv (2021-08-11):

Id | Designator | Package | Quantity | Designation | Supplier and ref
1 | R6 | R_0805_2012Metric | 1 | 10k
2 | R5 | R_0805_2012Metric | 1 | 27k
3 | J2,J4,J6,J5,J3,J1 | KEYSTONE-1042 | 6 | KEYSTONE-1042
4 | Ref** | battery_version | 1 | Val**
5 | H3,H4,H2,H1 | MountingHole_3.2mm_M3_DIN965_PadMOD | 4 | MountingHole_Pad
6 | Ref** | pycubed_logo | 1 | Val**
7 | REF**,REF**,REF**,REF**,REF**,REF** | Fiducial_0.75mm_Mask1.5mm | 6 | Fiducial_0.75mm_Mask1.5mm
8 | TH1 | R_Axial_DIN0204_L3.6mm_D1.6mm_P5.08mm_Vertical | 1 | Thermistor
9 | J12 | PinHeader_1x01_P1.00mm_Vertical | 1 | Screw_Terminal_01x01
10 | TP4,TP3,TP2,TP1 | TestPoint_Loop_D1.80mm_Drill1.0mm_Beaded | 4 | TestPoint
11 | C3,C4,C2,C1 | C_0603_1608Metric | 4 | 0.1uF
12 | R4 | R_0603_1608Metric | 1 | 1K
13 | R2,R1 | R_0603_1608Metric | 2 | 330
14 | R3 | R_2512_6332Metric | 1 | 0.01
15 | Q2,Q1 | SOIC-8_3.9x4.9mm_P1.27mm | 2 | IRF7458
16 | U1 | SOT95P280X130-6N | 1 | R5460N233AF
17 | J7,J8,J10 | Molex_Pico-Lock_503763-0291_1x02-1MP_P1.00m_Horizontal | 3 | Conn_01x02_Female
18 | J9,J11 | Molex_Pico-Lock_503763-0491_1x04-1MP_P1.00mm_Horizontal | 2 | Conn_01x04_Female
19 | U2 | TMP36FSZ-REEL | 1 | TMP36FSZ-REEL

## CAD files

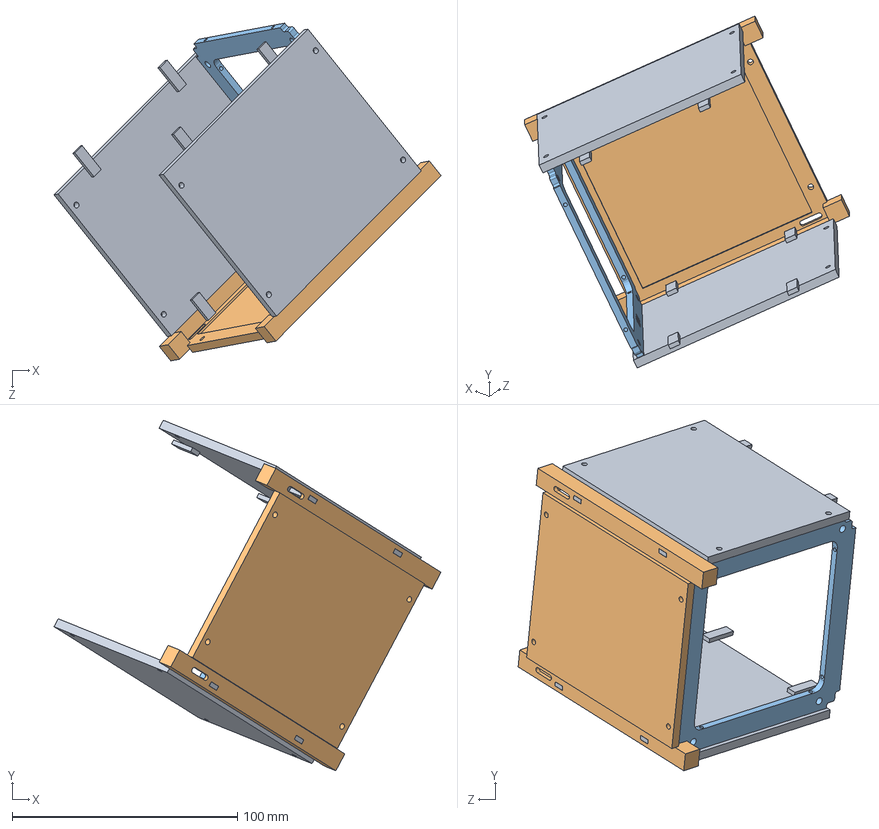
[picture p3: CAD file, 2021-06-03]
CAD Models/Artemis V2.SLDASM
171.6 x 155.5 x 149.8 mm
Side Panel inner V2 x 2
Side PanelV2
End cap

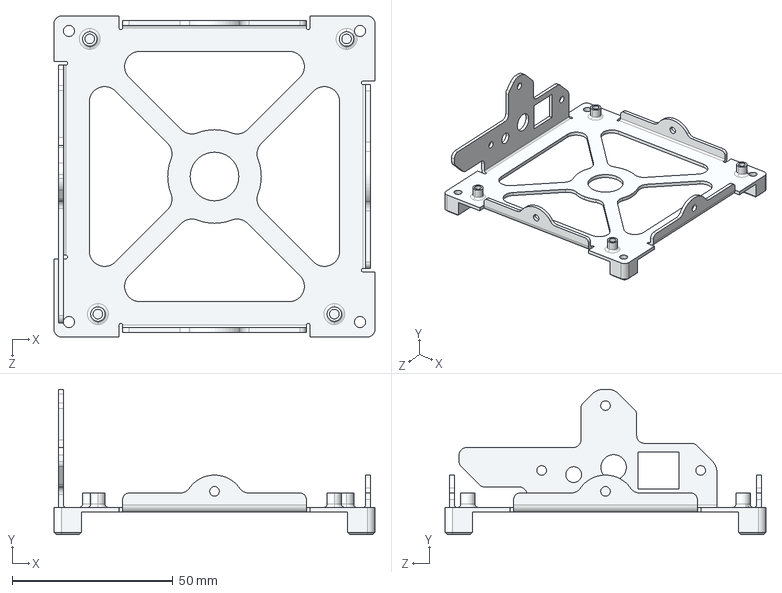
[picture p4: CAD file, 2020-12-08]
CAD Models/Hiapo 3D Print Structure/STEP/bottom.STEP
100.0 x 45.3 x 100.0 mm

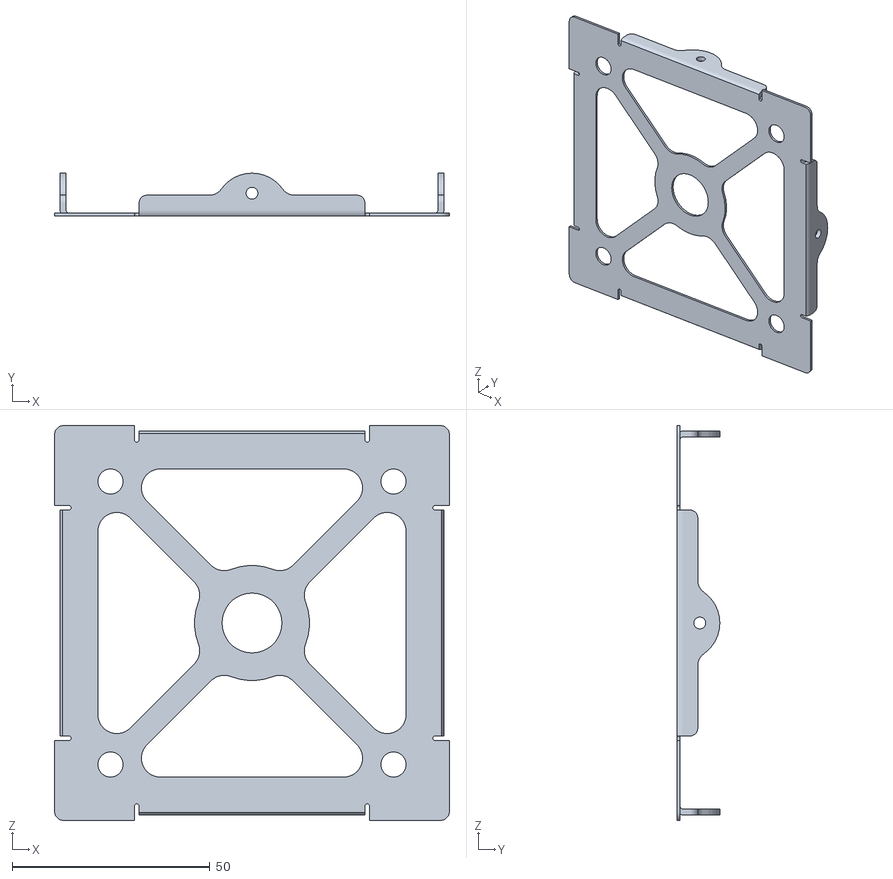
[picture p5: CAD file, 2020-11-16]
CAD Models/Hiapo 3D Print Structure/STL (already prepped for printing)/top1.STL
100.0 x 10.8 x 100.0

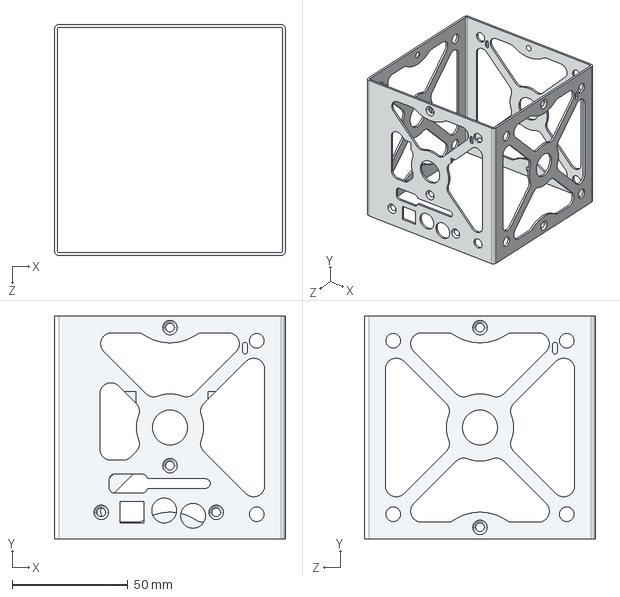
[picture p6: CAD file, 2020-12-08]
CAD Models/Hiapo 3D Print Structure/STEP/mid_skeletonized.STEP
100.0 x 96.5 x 100.0 mm

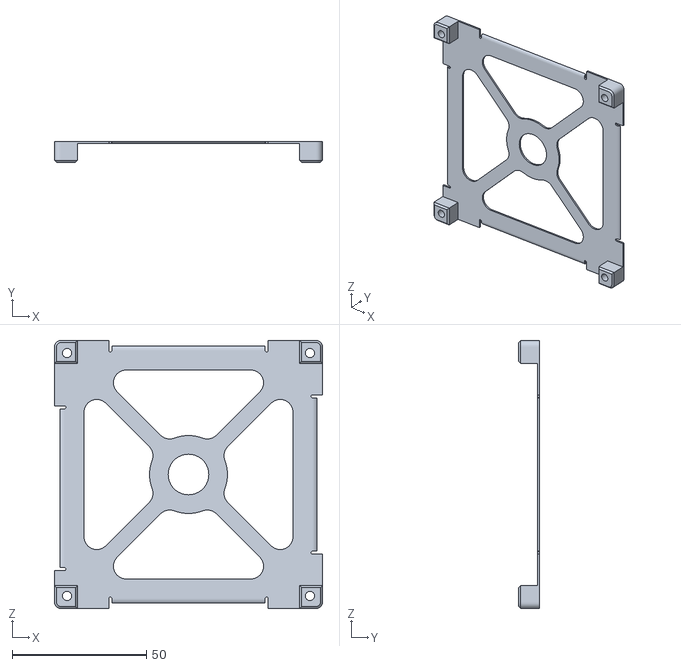
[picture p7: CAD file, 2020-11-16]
CAD Models/Hiapo 3D Print Structure/STL (already prepped for printing)/bottom2.STL
100.0 x 7.76 x 100.0

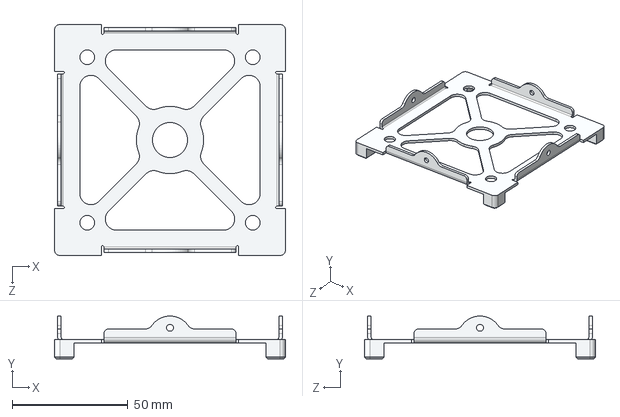
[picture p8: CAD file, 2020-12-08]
CAD Models/Hiapo 3D Print Structure/STEP/top.STEP
100.0 x 18.6 x 100.0 mm

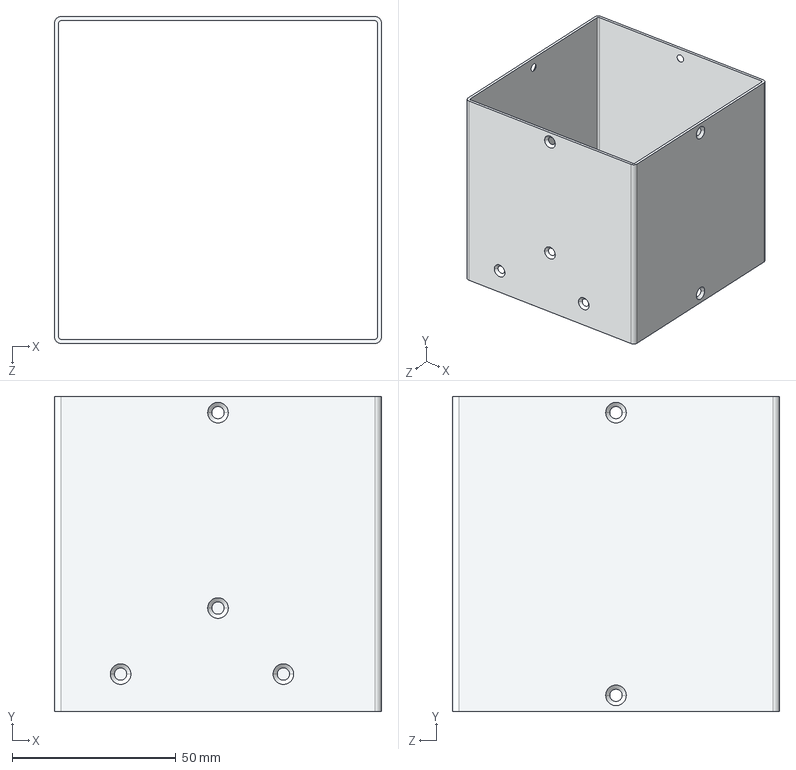
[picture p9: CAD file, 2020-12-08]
CAD Models/Hiapo 3D Print Structure/STEP/mid.STEP
100.0 x 96.5 x 100.0 mm

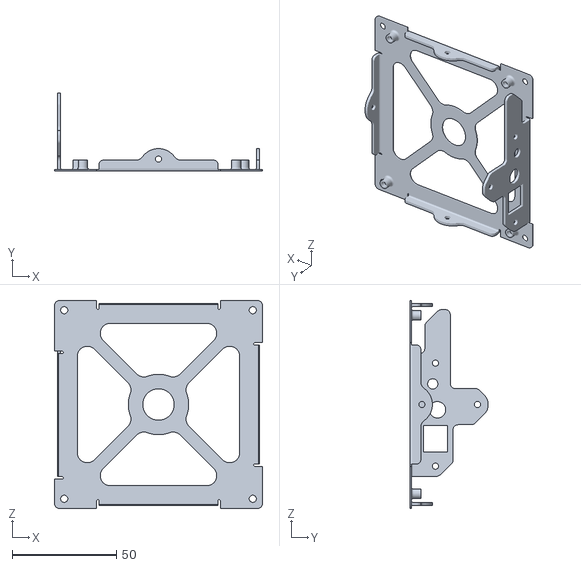
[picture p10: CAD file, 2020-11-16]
CAD Models/Hiapo 3D Print Structure/STL (already prepped for printing)/bottom1.STL
100.0 x 37.5 x 100.0

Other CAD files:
Thermal/artemis_thermal_lab.dwg
CAD Models/Hiapo 3D Print Structure/STL (already prepped for printing)/top2.STL
CAD Models/Hiapo 3D Print Structure/STL (already prepped for printing)/mid.STL

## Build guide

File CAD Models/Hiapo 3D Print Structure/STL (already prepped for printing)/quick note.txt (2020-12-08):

The top and bottom parts of the satellite have been split in half. These are meant to be glued together after
printing to produce a better looking model -kenny :)

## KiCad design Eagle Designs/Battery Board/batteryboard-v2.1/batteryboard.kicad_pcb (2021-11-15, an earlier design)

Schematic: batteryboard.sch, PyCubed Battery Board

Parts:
C1, C2, C3, C4, C5: 0.1uF; C_0603_1608Metric
H1, H2, H3, H4: MountingHole_Pad; MountingHole_3.2mm_M3_DIN965_PadMOD
J1, J2, J3, J4, J5, J6: KEYSTONE-1042; Manufacturer_Part_Number 1042; Mouser Part Number 534-1042
J7, J8, J10: Conn_01x02_Female; Molex_Pico-Lock_503763-0291_1x02-1MP_P1.00m_Horizontal
J9, J11: Conn_01x04_Female; Molex_Pico-Lock_503763-0491_1x04-1MP_P1.00mm_Horizontal
J12: Screw_Terminal_01x01; PinHeader_1x01_P1.00mm_Vertical
Q1, Q2: IRF7458; SOIC-8_3.9x4.9mm_P1.27mm
R1, R2: 330; R_0603_1608Metric
R3: 0.01; R_2512_6332Metric
R4: 1K; R_0603_1608Metric
R5: 45.3k; R_0805_2012Metric
R6: 10k; R_0805_2012Metric
TH1: Thermistor; R_Axial_DIN0204_L3.6mm_D1.6mm_P5.08mm_Vertical
TP1, TP2, TP3, TP4: TestPoint; TestPoint_Loop_D1.80mm_Drill1.0mm_Beaded
U1: R5460N233AF; SOT95P280X130-6N; Manufacturer_Part_Number R5460N233AF-TR-FE; Mouser Part Number 848-R5460N233AFTRFE
U2: TMP36FSZ; SOIC8P127_490X600X175L83X41N

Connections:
/VDD: C1.2, R1.2, U1.5
B-: C1.1, C2.1, C4.1, J1.1, J3.1, J5.1, R3.1, TP1.1, U1.6
BAT_THERM: J12.1, TH1.1
BM: J1.2, J2.1, J3.2, J4.1, J5.2, J6.1, R2.1, TP2.1
GND: C5.2, J11.3, J11.4, R6.2, U2.4 (GND)
unnamed: C2.2, R2.2, U1.4
unnamed: C3.1, Q1.1 (S), Q1.2 (S), Q1.3 (S), R3.2
unnamed: C4.2, R4.1, U1.3
unnamed: C5.1, J11.1, U2.5 (~SHUTDOWN), U2.8 (+VS)
unnamed: J7.1, J8.1, J9.1, J9.3, J10.2
unnamed: J11.2, R5.2, R6.1
unnamed: Q1.4 (G), U1.1
unnamed: Q1.5 (D), Q1.6 (D), Q1.7 (D), Q1.8 (D), Q2.5 (D), Q2.6 (D), Q2.7 (D), Q2.8 (D)
unnamed: Q2.4 (G), U1.2
unnamed: R5.1, U2.1 (VOUT)
PACK+: J2.2, J4.2, J6.2, J10.1, R1.1, TP4.1
PACK-: C3.2, H1.1, H2.1, H3.1, H4.1, J7.2, J8.2, J9.2, J9.4, Q2.1 (S), Q2.2 (S), Q2.3 (S), R4.2, TH1.2, TP3.1

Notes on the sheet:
Must install low-side before high-side
One from this group first
OPTIONAL
Test Points
BATTERY PROTECTION IC
PyCubed Battery Board
Temp Sensor

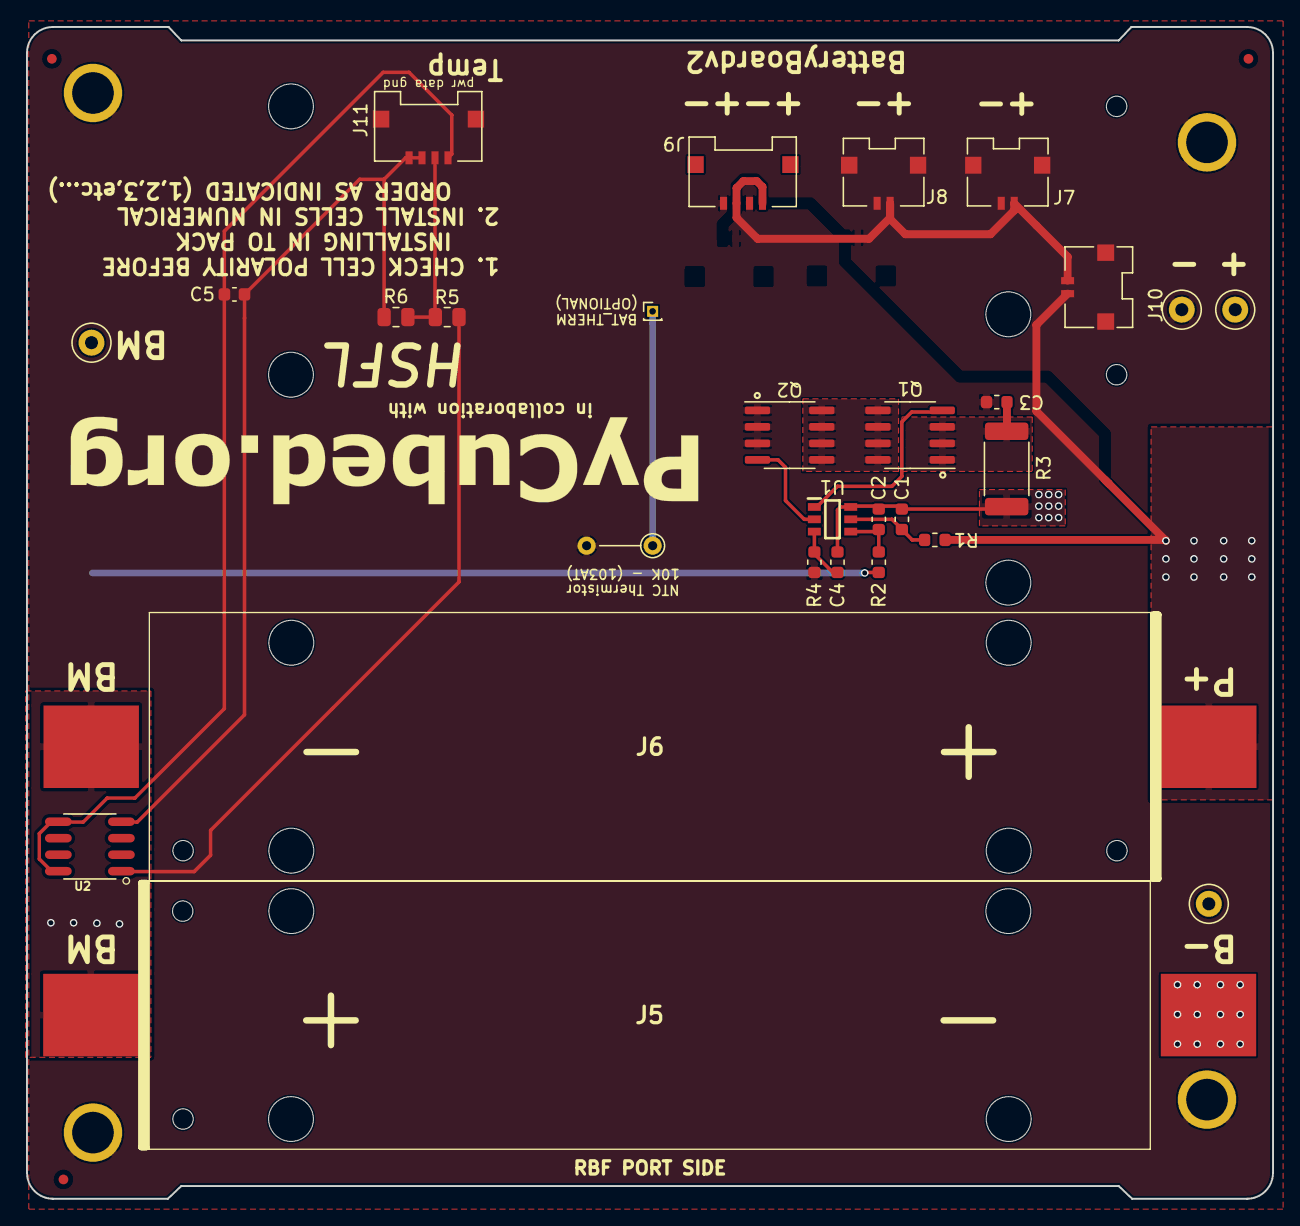
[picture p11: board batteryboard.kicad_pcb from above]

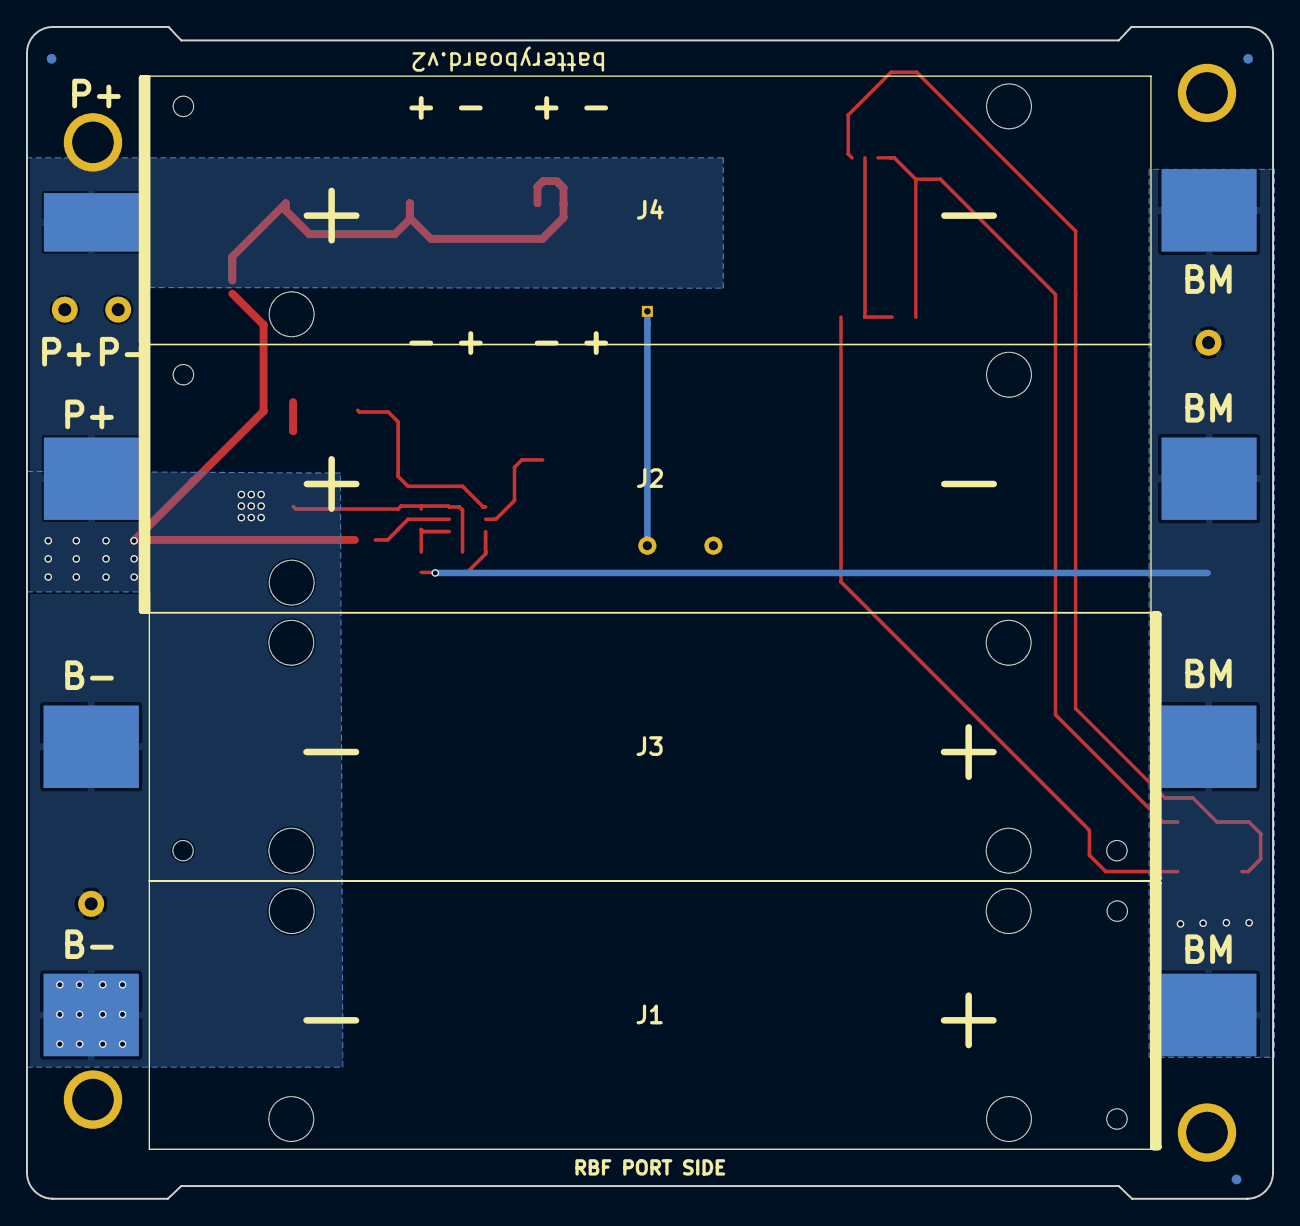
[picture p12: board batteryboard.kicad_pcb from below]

Board: 2 copper layers, 95.9 x 90.2 mm, 37 parts (4 on the bottom side), 17 nets.

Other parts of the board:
Ref**: Val**; pycubed_logo

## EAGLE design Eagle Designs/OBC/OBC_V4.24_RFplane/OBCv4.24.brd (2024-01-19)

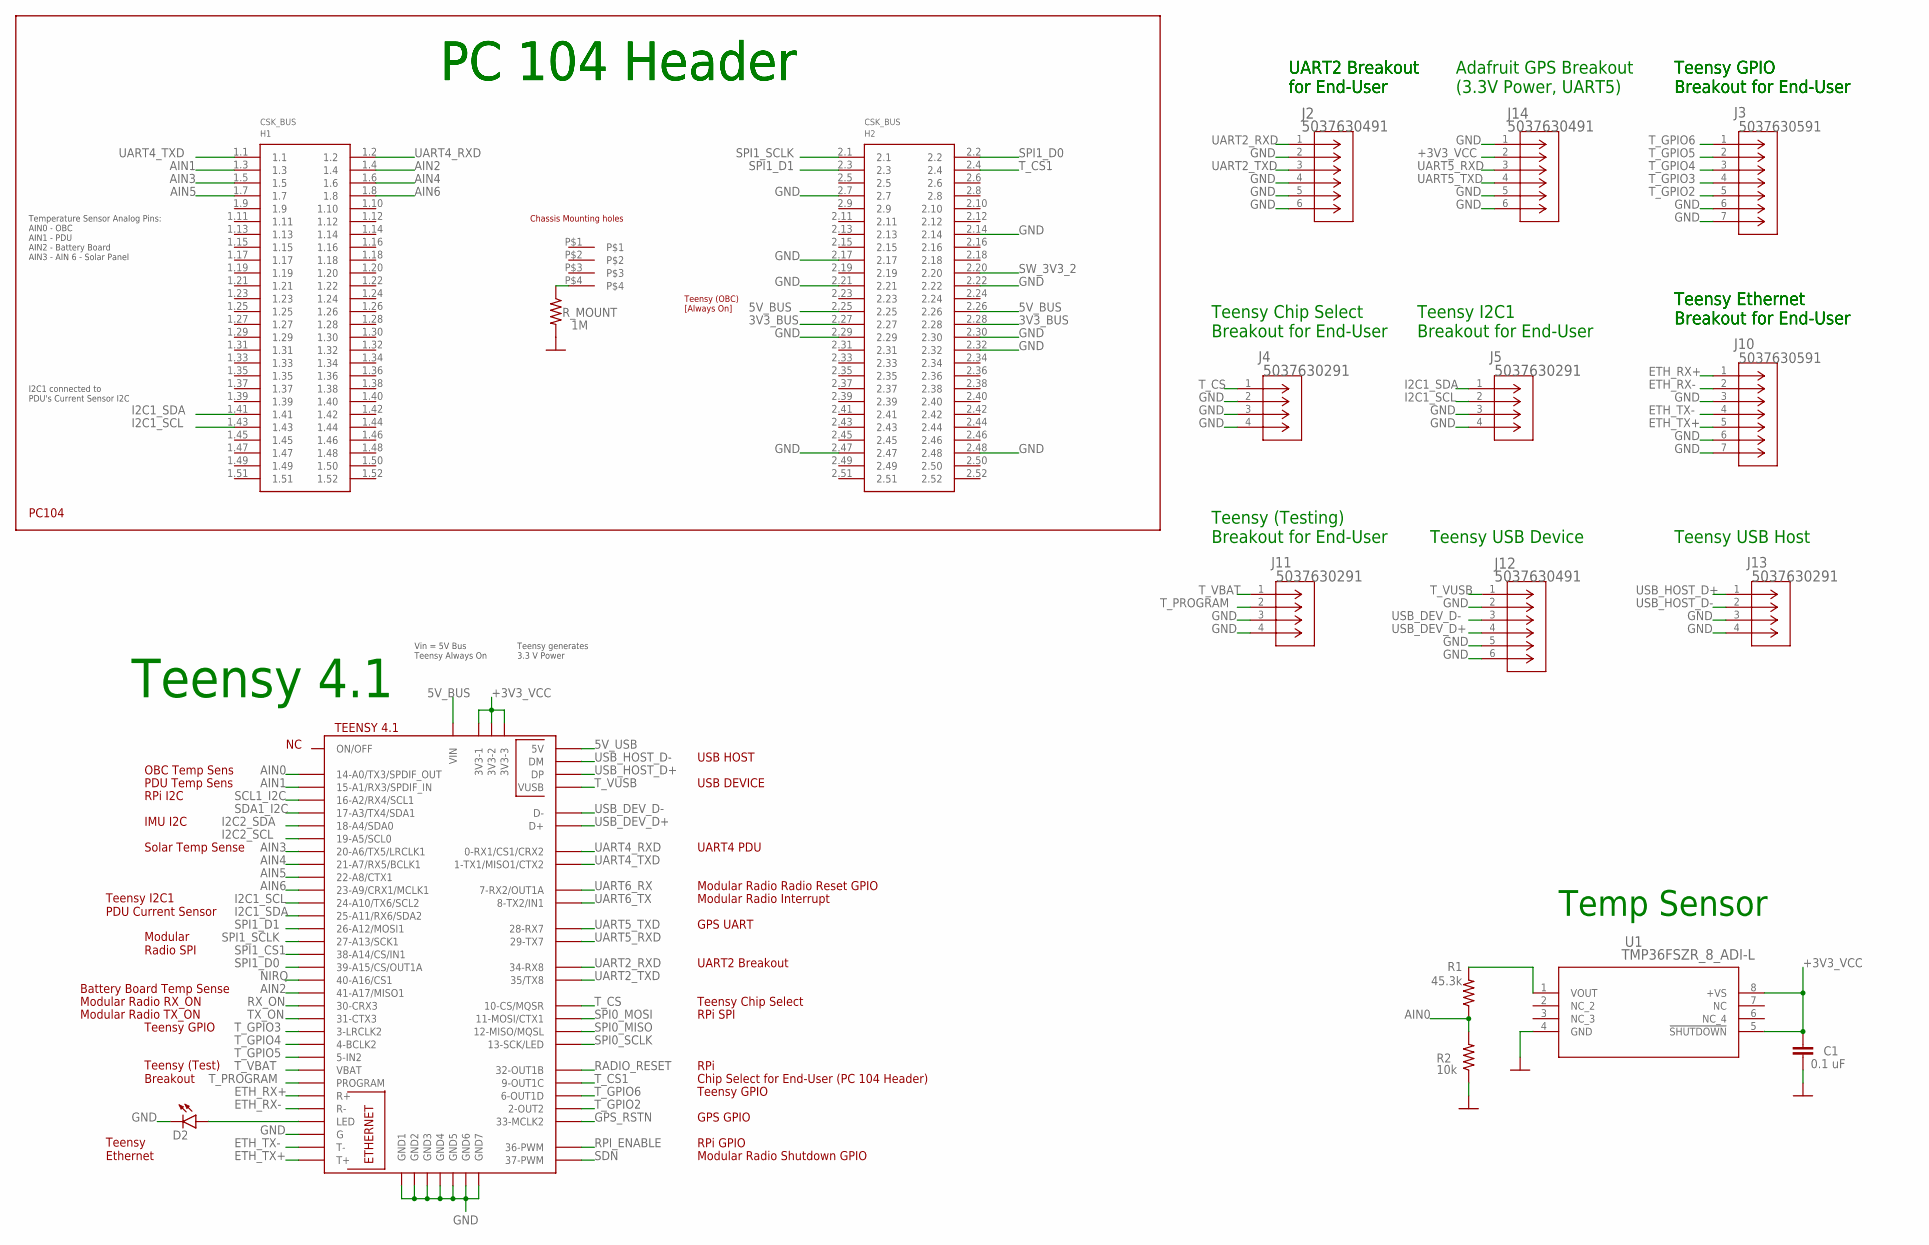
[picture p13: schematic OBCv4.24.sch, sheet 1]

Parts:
C1: 0.1 uF; 0805
D2: LEDCHIP-LED0603; CHIP-LED0603
H1: PC104_WCONN
J2, J12, J14: 5037630491; CON_5037630491
J3, J10: 5037630591; CON_5037630591
J4, J5, J11, J13: 5037630291; CON_5037630291
R1: 45.3k; 0805
R2: 10k; 0805
R_MOUNT: 1M; 0805
U1: TMP36FSZR_8_ADI-L; R_8_ADI-L
U$1: TEENSY41TEENSY; TEENSY41

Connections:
3V3_BUS: H1.2.27, H1.2.28; also elsewhere on the board
5V_BUS: H1.2.25, H1.2.26, U$1.VIN; also elsewhere on the board
5V_USB: U$1.+5V (5V)
+3V3_VCC: C1.1, J14.2, U1.5 (!SHUTDOWN), U1.8 (+VS), U$1.3V3-1, U$1.3V3-2, U$1.3V3-3; also elsewhere on the board
AIN0: R1.1, R2.2, U$1.14-A0/TX3/SPDIF_OUT
AIN1: H1.1.3, U$1.15-A1/RX3/SPDIF_IN
AIN2: H1.1.4, U$1.41-A17/MISO1
AIN3: H1.1.5, U$1.20-A6/TX5/LRCLK1
AIN4: H1.1.6, U$1.21-A7/RX5/BCLK1
AIN5: H1.1.7, U$1.22-A8/CTX1
AIN6: H1.1.8, U$1.23-A9/CRX1/MCLK1
ETH_RX+: J10.1, U$1.R+
ETH_RX-: J10.2, U$1.R-
ETH_TX+: J10.5, U$1.T+
ETH_TX-: J10.4, U$1.T-
GND: C1.2, D2.C, H1.2.7, H1.2.14, H1.2.17, H1.2.21, H1.2.22, H1.2.29, H1.2.30, H1.2.32, H1.2.47, H1.2.48, J2.2, J2.4, J2.5, J2.6, J3.6, J3.7, J4.2, J4.3, J4.4, J5.3, J5.4, J10.3, J10.6, J10.7, J11.3, J11.4, J12.2, J12.5, J12.6, J13.3, J13.4, J14.1, J14.5, J14.6, R2.1, R_MOUNT.2, U1.4 (GND), U$1.G, U$1.GND (GND7), U$1.GND1, U$1.GND2, U$1.GND3, U$1.GND4, U$1.GND5, U$1.GND6; also elsewhere on the board
GPS_RSTN: U$1.33-MCLK2; also elsewhere on the board
I2C1_SCL: H1.1.43, J5.2, U$1.24-A10/TX6/SCL2
I2C1_SDA: H1.1.41, J5.1, U$1.25-A11/RX6/SDA2
I2C2_SCL: U$1.19-A5/SCL0; also elsewhere on the board
I2C2_SDA: U$1.18-A4/SDA0; also elsewhere on the board
unnamed: D2.A, U$1.LED
unnamed: R1.2, U1.1 (VOUT)
unnamed: H1.P$4, R_MOUNT.1
NIRQ: U$1.40-A16/CS1; also elsewhere on the board
RADIO_RESET: U$1.32-OUT1B; also elsewhere on the board
RPI_ENABLE: U$1.36-PWM; also elsewhere on the board
RX_ON: U$1.30-CRX3; also elsewhere on the board
SCL1_I2C: U$1.16-A2/RX4/SCL1; also elsewhere on the board
SDA1_I2C: U$1.17-A3/TX4/SDA1; also elsewhere on the board
SDN: U$1.37-PWM; also elsewhere on the board
SPI0_MISO: U$1.12-MISO/MQSL; also elsewhere on the board
SPI0_MOSI: U$1.11-MOSI/CTX1; also elsewhere on the board
SPI0_SCLK: U$1.13-SCK/LED; also elsewhere on the board
SPI1_CS1: U$1.38-A14/CS/IN1; also elsewhere on the board
SPI1_D0: H1.2.2, U$1.39-A15/CS/OUT1A; also elsewhere on the board
SPI1_D1: H1.2.3, U$1.26-A12/MOSI1; also elsewhere on the board
SPI1_SCLK: H1.2.1, U$1.27-A13/SCK1; also elsewhere on the board
SW_3V3_2: H1.2.20; also elsewhere on the board
TX_ON: U$1.31-CTX3; also elsewhere on the board
T_CS: J4.1, U$1.10-CS\MQSR (10-CS/MQSR)
T_CS1: H1.2.4, U$1.9-OUT1C
T_GPIO2: J3.5, U$1.2-OUT2
T_GPIO3: J3.4, U$1.3-LRCLK2
T_GPIO4: J3.3, U$1.4-BCLK2
T_GPIO5: J3.2, U$1.5-IN2
T_GPIO6: J3.1, U$1.6-OUT1D
T_PROGRAM: J11.2, U$1.PROGRAM
T_VBAT: J11.1, U$1.VBAT
T_VUSB: J12.1, U$1.VUSB
UART2_RXD: J2.1, U$1.34-RX8
UART2_TXD: J2.3, U$1.35-TX8 (35/TX8)
UART4_RXD: H1.1.2, U$1.0-RX1/CS1/CRX2
UART4_TXD: H1.1.1, U$1.1-TX1/MISO1/CTX2
UART5_RXD: J14.3, U$1.29-TX7; also elsewhere on the board
UART5_TXD: J14.4, U$1.28-RX7; also elsewhere on the board
UART6_RX: U$1.7-RX2/OUT1A; also elsewhere on the board
UART6_TX: U$1.8-TX2/IN1; also elsewhere on the board
USB_DEV_D+: J12.4, U$1.D+
USB_DEV_D-: J12.3, U$1.D-
USB_HOST_D+: J13.1, U$1.DP
USB_HOST_D-: J13.2, U$1.DM

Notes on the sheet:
Temp Sensor
PC 104 Header
Temperature Sensor Analog Pins: AIN0 - OBC AIN1 - PDU AIN2 - Battery Board AIN3 - AIN 6 - Solar Panel
UART2 Breakout for End-User
Teensy 4.1
Teensy GPIO Breakout for End-User
Teensy Chip Select Breakout for End-User
Teensy I2C1 Breakout for End-User
OBC Temp Sens
PDU Temp Sens
RPi I2C
IMU I2C
Solar Temp Sense
Teensy I2C1 PDU Current Sensor
Modular Radio SPI
Battery Board Temp Sense
Teensy GPIO
Teensy (Test) Breakout
Teensy Ethernet
RPi GPIO
GPS GPIO
RPi SPI
Teensy Chip Select
UART2 Breakout
GPS UART
Modular Radio Radio Reset GPIO
UART4 PDU
USB HOST
USB DEVICE
Teensy Ethernet Breakout for End-User
Teensy (Testing) Breakout for End-User
Teensy USB Device
Teensy USB Host
Teensy (OBC) [Always On]
Vin = 5V Bus Teensy Always On
Teensy generates 3.3 V Power
Adafruit GPS Breakout (3.3V Power, UART5)
Modular Radio Interrupt
I2C1 connected to PDU's Current Sensor I2C
Chip Select for End-User (PC 104 Header)

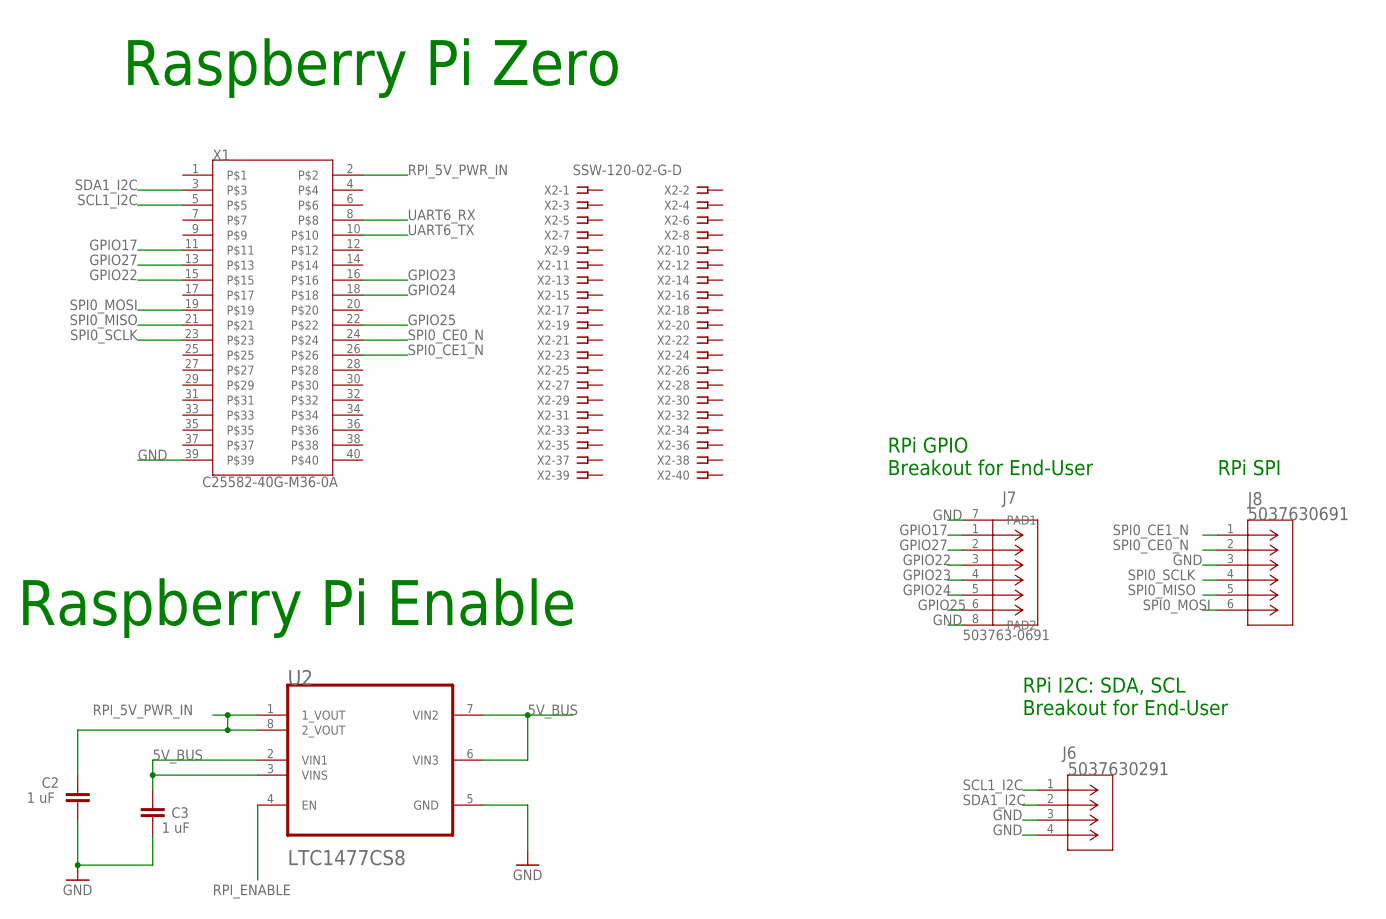
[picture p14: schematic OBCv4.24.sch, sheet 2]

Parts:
C2, C3: 1 uF; 0805
J6: 5037630291; CON_5037630291
J7: 503763-0691; CONN_503763-0691_MOL
J8: 5037630691; CONN_503763-0691_MOL
U2: LTC1477CS8LINEAR_TECHNOLOGY_LTC1477CS8_0_2; LINEAR_TECHNOLOGY_LTC1477CS8_2
X1: C25582-40G-M36-0A; ADAFRUIT_C25582-40G-M36-0A_0
X2: SSW-120-02-G-D

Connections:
5V_BUS: C3.1, U2.2 (VIN1), U2.3 (VINS), U2.6 (VIN3), U2.7 (VIN2); also elsewhere on the board
GND: C2.2, C3.2, J6.3, J6.4, J7.7 (PAD1), J7.8 (PAD2), J8.3, U2.5 (GND), X1.39; also elsewhere on the board
GPIO17: J7.1, X1.11
GPIO22: J7.3, X1.15
GPIO23: J7.4, X1.16
GPIO24: J7.5, X1.18
GPIO25: J7.6, X1.22
GPIO27: J7.2, X1.13
RPI_5V_PWR_IN: C2.1, U2.1 (1_VOUT), U2.8 (2_VOUT), X1.2
RPI_ENABLE: U2.4 (EN); also elsewhere on the board
SCL1_I2C: J6.1, X1.5; also elsewhere on the board
SDA1_I2C: J6.2, X1.3; also elsewhere on the board
SPI0_CE0_N: J8.2, X1.24
SPI0_CE1_N: J8.1, X1.26
SPI0_MISO: J8.5, X1.21; also elsewhere on the board
SPI0_MOSI: J8.6, X1.19; also elsewhere on the board
SPI0_SCLK: J8.4, X1.23; also elsewhere on the board
UART6_RX: X1.8; also elsewhere on the board
UART6_TX: X1.10; also elsewhere on the board

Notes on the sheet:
Raspberry Pi Zero
Raspberry Pi Enable
RPi I2C: SDA, SCL Breakout for End-User
RPi GPIO Breakout for End-User
RPi SPI

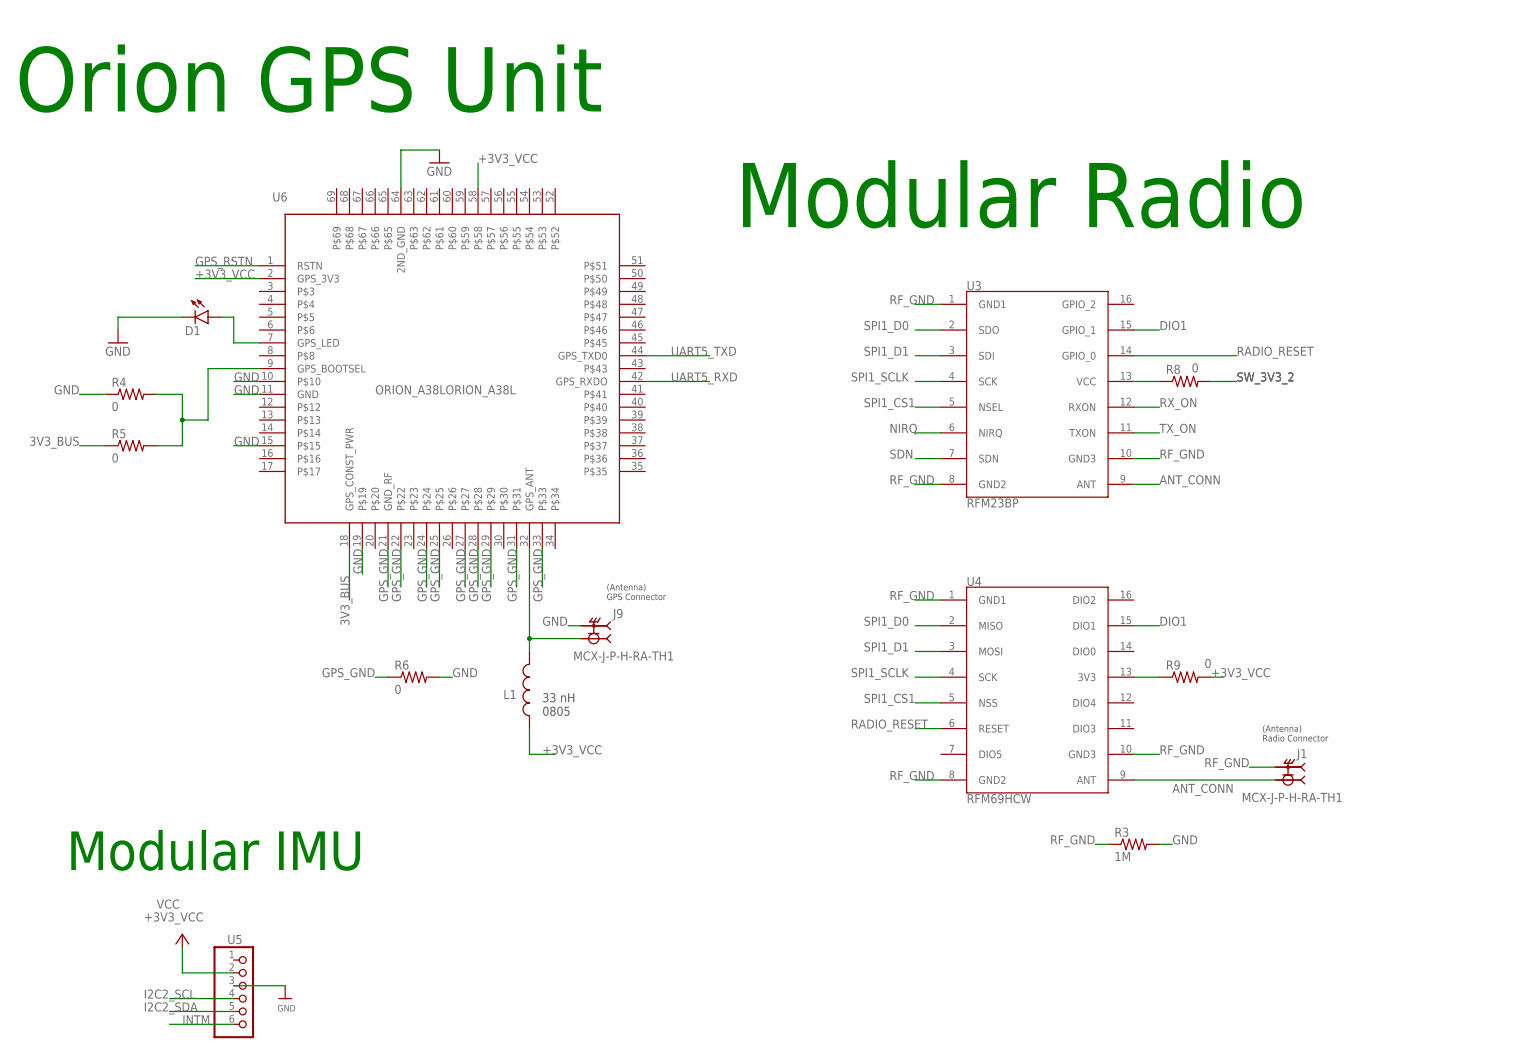
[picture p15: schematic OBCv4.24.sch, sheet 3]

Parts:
D1: LEDCHIP-LED0603; CHIP-LED0603
J1, J9: MCX-J-P-H-RA-TH1; SAMTEC_MCX-J-P-H-RA-TH1
L1: AIMC-0805-2N2S-T; INDC2012X105N
R3: 1M; 0805
R4, R5, R6: 0; 0805
R8, R9: 0; R2512
U3: RFM23BP
U4: RFM69HCW
U5: HEADER-1X670MIL; 1X06_ROUND_70
U6: ORION_A38LORION_A38L; ORION_A38L

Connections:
3V3_BUS: R5.1, U6.18 (GPS_CONST_PWR); also elsewhere on the board
+3V3_VCC: L1.1, R9.2, U5.2, U6.2 (GPS_3V3), U6.58; also elsewhere on the board
ANT_CONN: J1.1, U3.9 (ANT), U4.9 (ANT)
DIO1: U3.15 (GPIO_1), U4.15 (DIO1)
GND: D1.C, J9.S1 (2), J9.S2 (2), J9.S3 (2), J9.S4 (2), R3.2, R4.1, R6.2, U5.3, U6.10, U6.11 (GND), U6.15, U6.19, U6.64 (2ND_GND); also elsewhere on the board
GPS_GND: R6.1, U6.21 (GND_RF), U6.22, U6.24, U6.25, U6.27, U6.28, U6.29, U6.31, U6.33
GPS_RSTN: U6.1 (RSTN); also elsewhere on the board
I2C2_SCL: U5.4; also elsewhere on the board
I2C2_SDA: U5.5; also elsewhere on the board
INTM: U5.6
unnamed: R8.1, U3.13 (VCC)
unnamed: R9.1, U4.13 (3V3)
unnamed: R4.2, R5.2, U6.9 (GPS_BOOTSEL)
unnamed: J9.1, L1.2, U6.32 (GPS_ANT)
unnamed: D1.A, U6.7 (GPS_LED)
NIRQ: U3.6 (NIRQ); also elsewhere on the board
RADIO_RESET: U3.14 (GPIO_0), U4.6 (RESET); also elsewhere on the board
RF_GND: J1.S1 (2), J1.S2 (2), J1.S3 (2), J1.S4 (2), R3.1, U3.1 (GND1), U3.8 (GND2), U3.10 (GND3), U4.1 (GND1), U4.8 (GND2), U4.10 (GND3)
RX_ON: U3.12 (RXON); also elsewhere on the board
SDN: U3.7 (SDN); also elsewhere on the board
SPI1_CS1: U3.5 (NSEL), U4.5 (NSS); also elsewhere on the board
SPI1_D0: U3.2 (SDO), U4.2 (MISO); also elsewhere on the board
SPI1_D1: U3.3 (SDI), U4.3 (MOSI); also elsewhere on the board
SPI1_SCLK: U3.4 (SCK), U4.4 (SCK); also elsewhere on the board
SW_3V3_2: R8.2; also elsewhere on the board
TX_ON: U3.11 (TXON); also elsewhere on the board
UART5_RXD: U6.42 (GPS_RXDO); also elsewhere on the board
UART5_TXD: U6.44 (GPS_TXD0); also elsewhere on the board

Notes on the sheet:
Orion GPS Unit
Modular Radio
Modular IMU
(Antenna) Radio Connector
(Antenna) GPS Connector
33 nH 0805

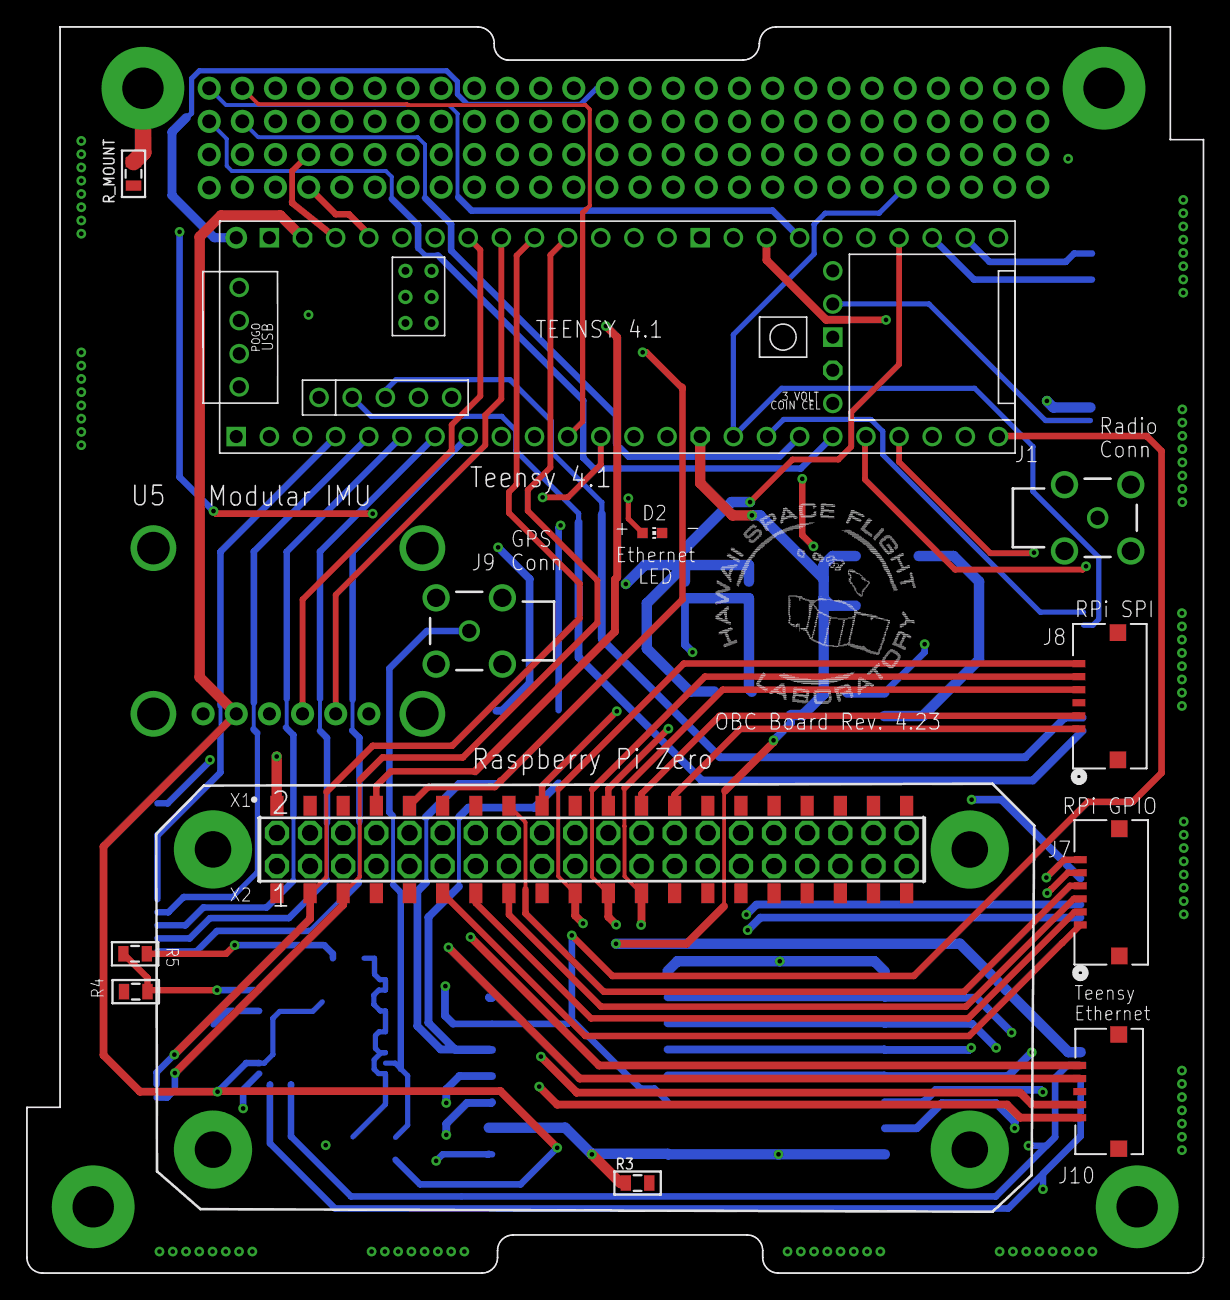
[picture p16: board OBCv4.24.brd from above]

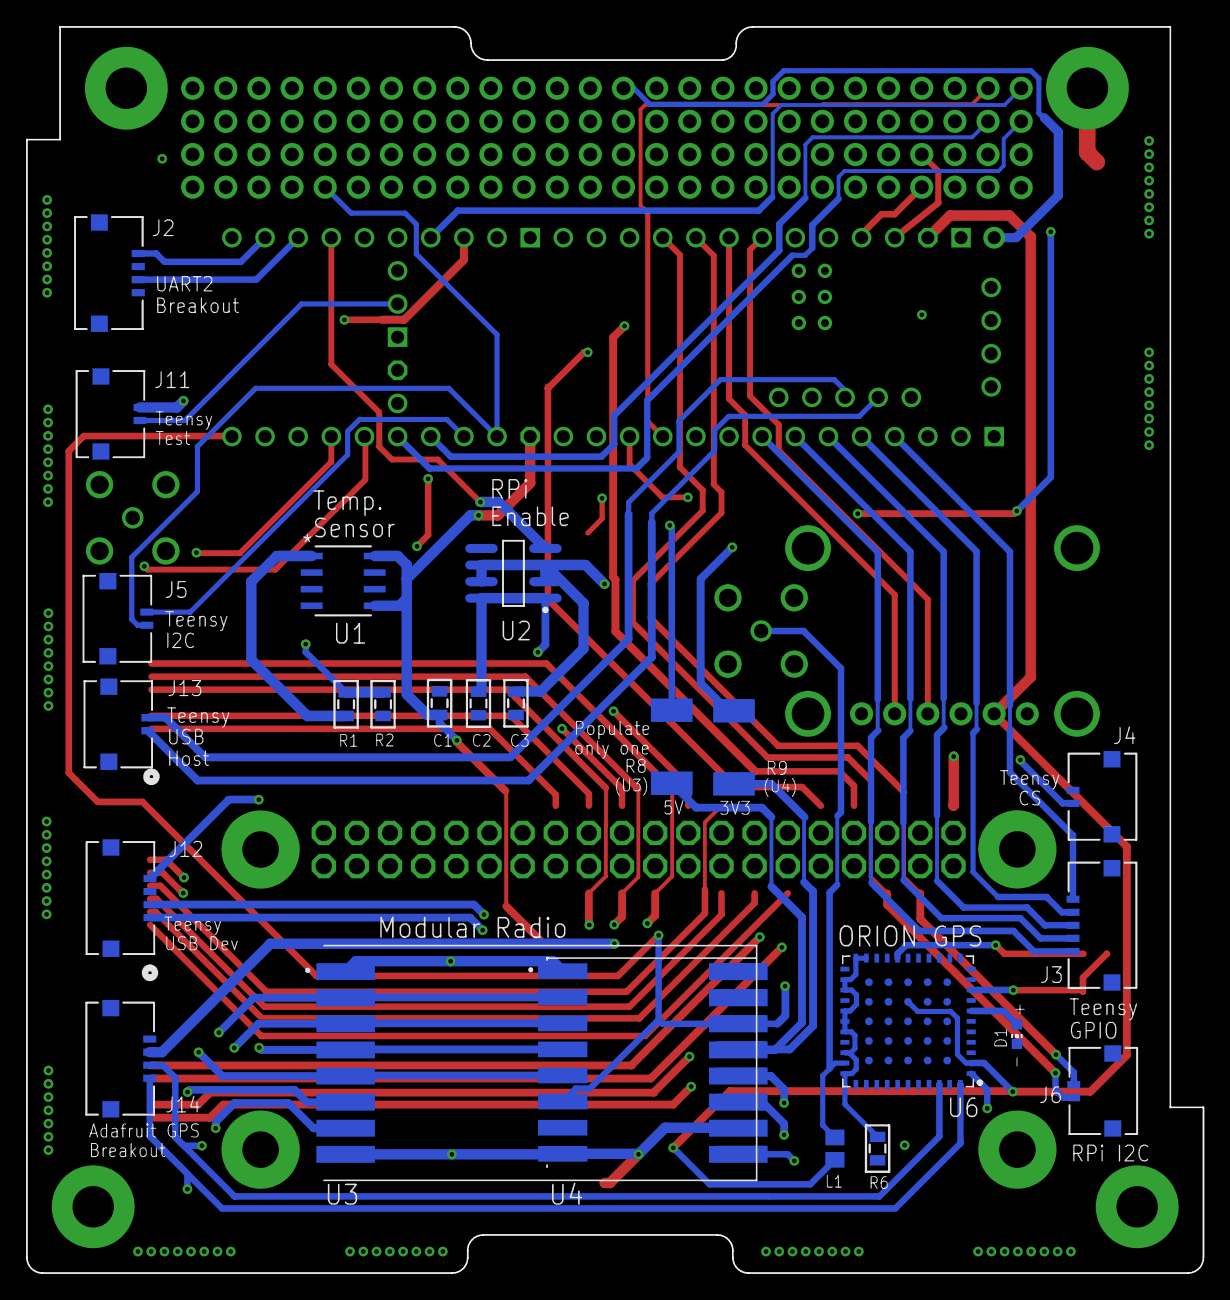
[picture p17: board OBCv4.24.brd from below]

Board: 4 copper layers, 90.2 x 95.5 mm, 39 parts (24 on the bottom side), 79 nets.

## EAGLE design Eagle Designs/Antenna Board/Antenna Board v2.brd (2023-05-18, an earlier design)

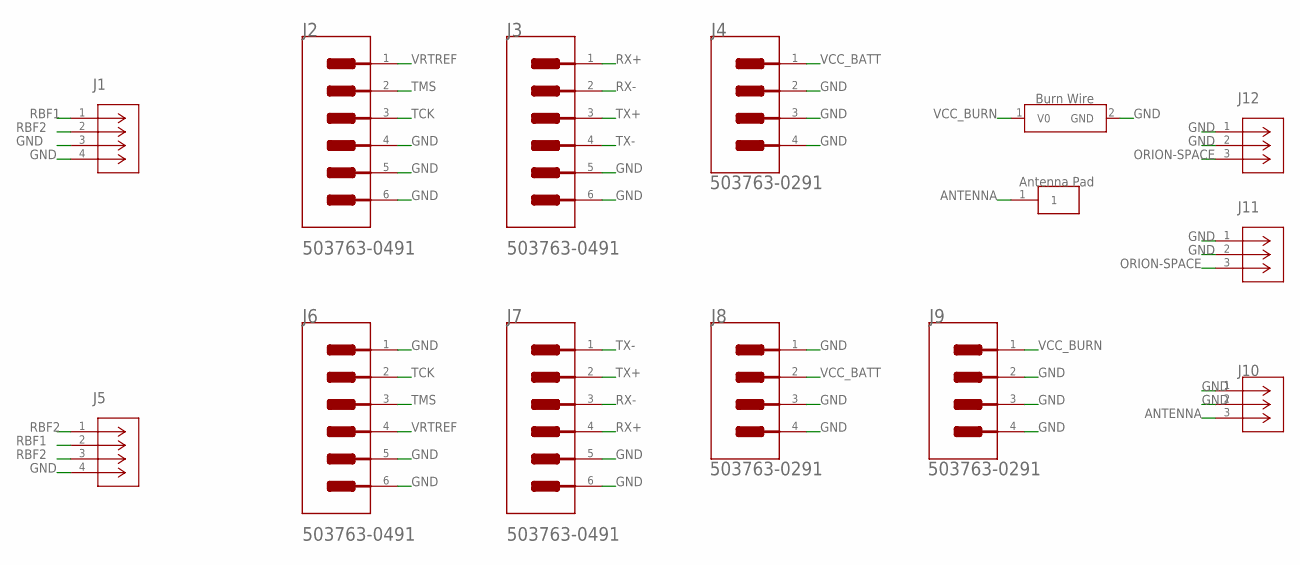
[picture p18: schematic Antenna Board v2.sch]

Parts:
J1, J5: 5037630291; CON_5037630291
J2, J3, J6, J7: MOLEX_503763-0491MOLEX_503763-0491_0_0; MOLEX_503763-0491_0
J4, J8, J9: MOLEX_503763-0291MOLEX_503763-0291_0_0; MOLEX_503763-0291_0
J10, J11, J12: U.FL-R-SMT-1(01); CONN_-SMT-1(01)
U$2: ANTENNA_PAD
U$3: BURNWIRE

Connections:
ANTENNA: J10.3, U$2.1
GND: J1.3, J1.4, J2.4, J2.5 (MNT_1), J2.6 (MNT_2), J3.5 (MNT_1), J3.6 (MNT_2), J4.2, J4.3 (MNT_1), J4.4 (MNT_2), J5.4, J6.1, J6.5 (MNT_1), J6.6 (MNT_2), J7.5 (MNT_1), J7.6 (MNT_2), J8.1, J8.3 (MNT_1), J8.4 (MNT_2), J9.2, J9.3 (MNT_1), J9.4 (MNT_2), J10.1, J10.2, J11.1, J11.2, J12.1, J12.2, U$3.2 (GND)
ORION-SPACE: J11.3, J12.3
RBF1: J1.1, J5.2
RBF2: J1.2, J5.1, J5.3
RX+: J3.1, J7.4
RX-: J3.2, J7.3
TCK: J2.3, J6.2
TMS: J2.2, J6.3
TX+: J3.3, J7.2
TX-: J3.4, J7.1
VCC_BATT: J4.1, J8.2
VCC_BURN: J9.1, U$3.1 (V0)
VRTREF: J2.1, J6.4

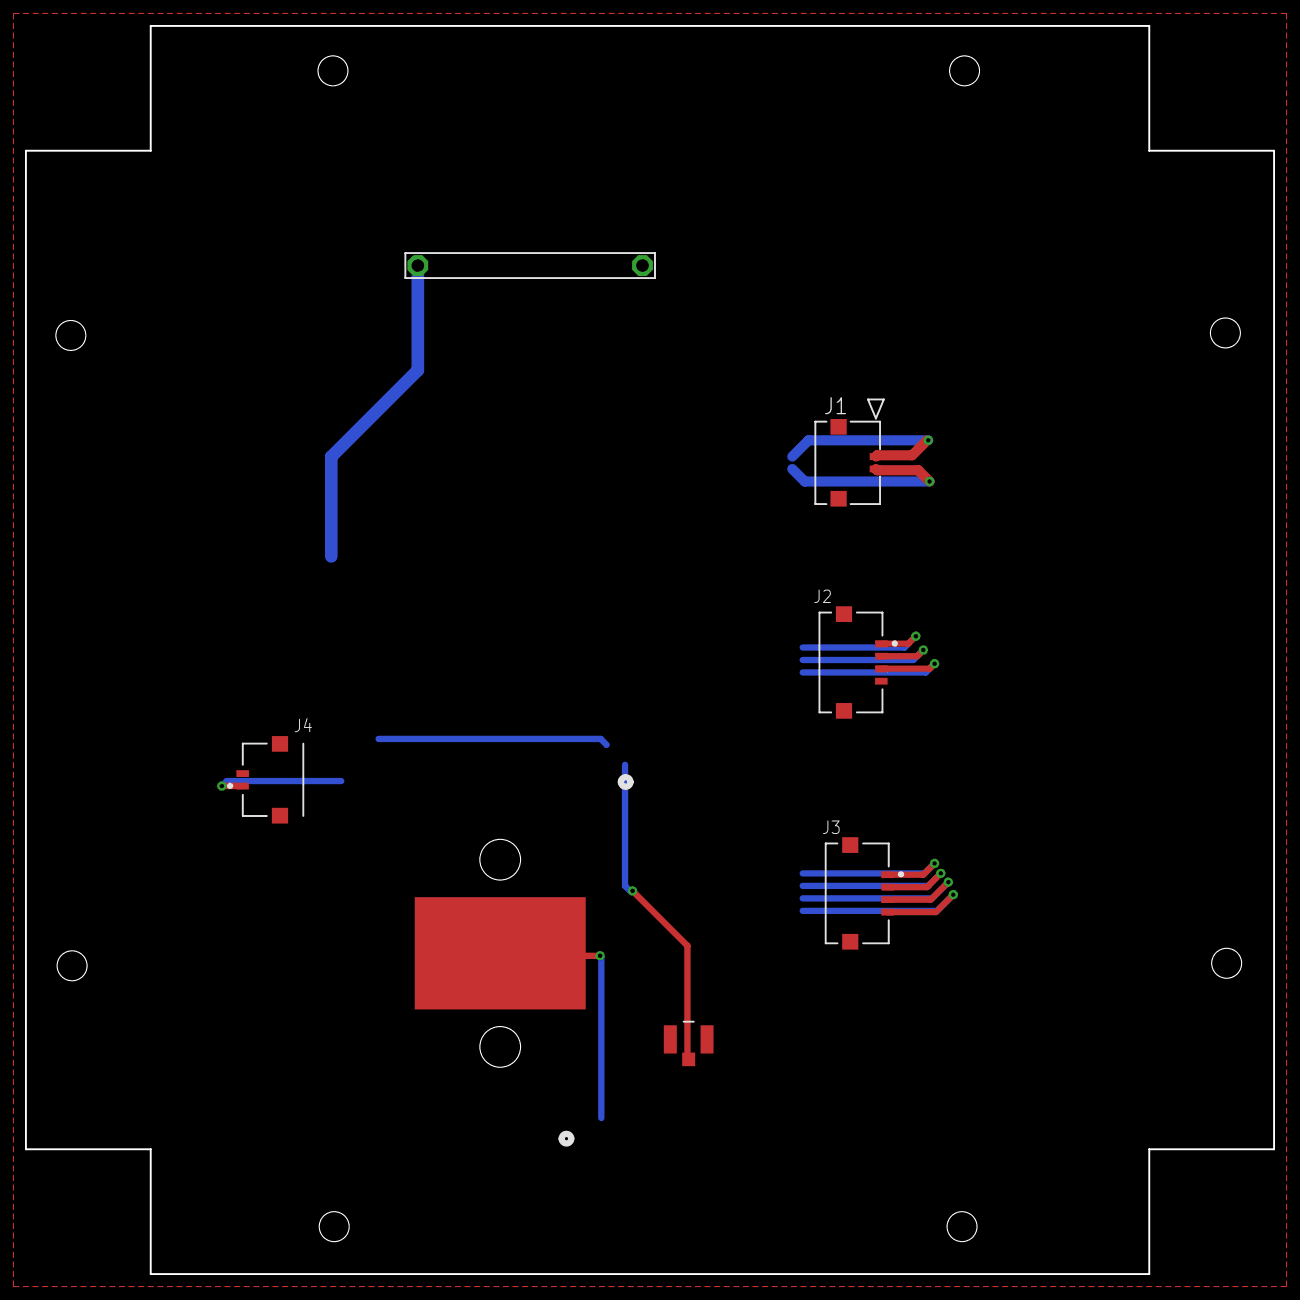
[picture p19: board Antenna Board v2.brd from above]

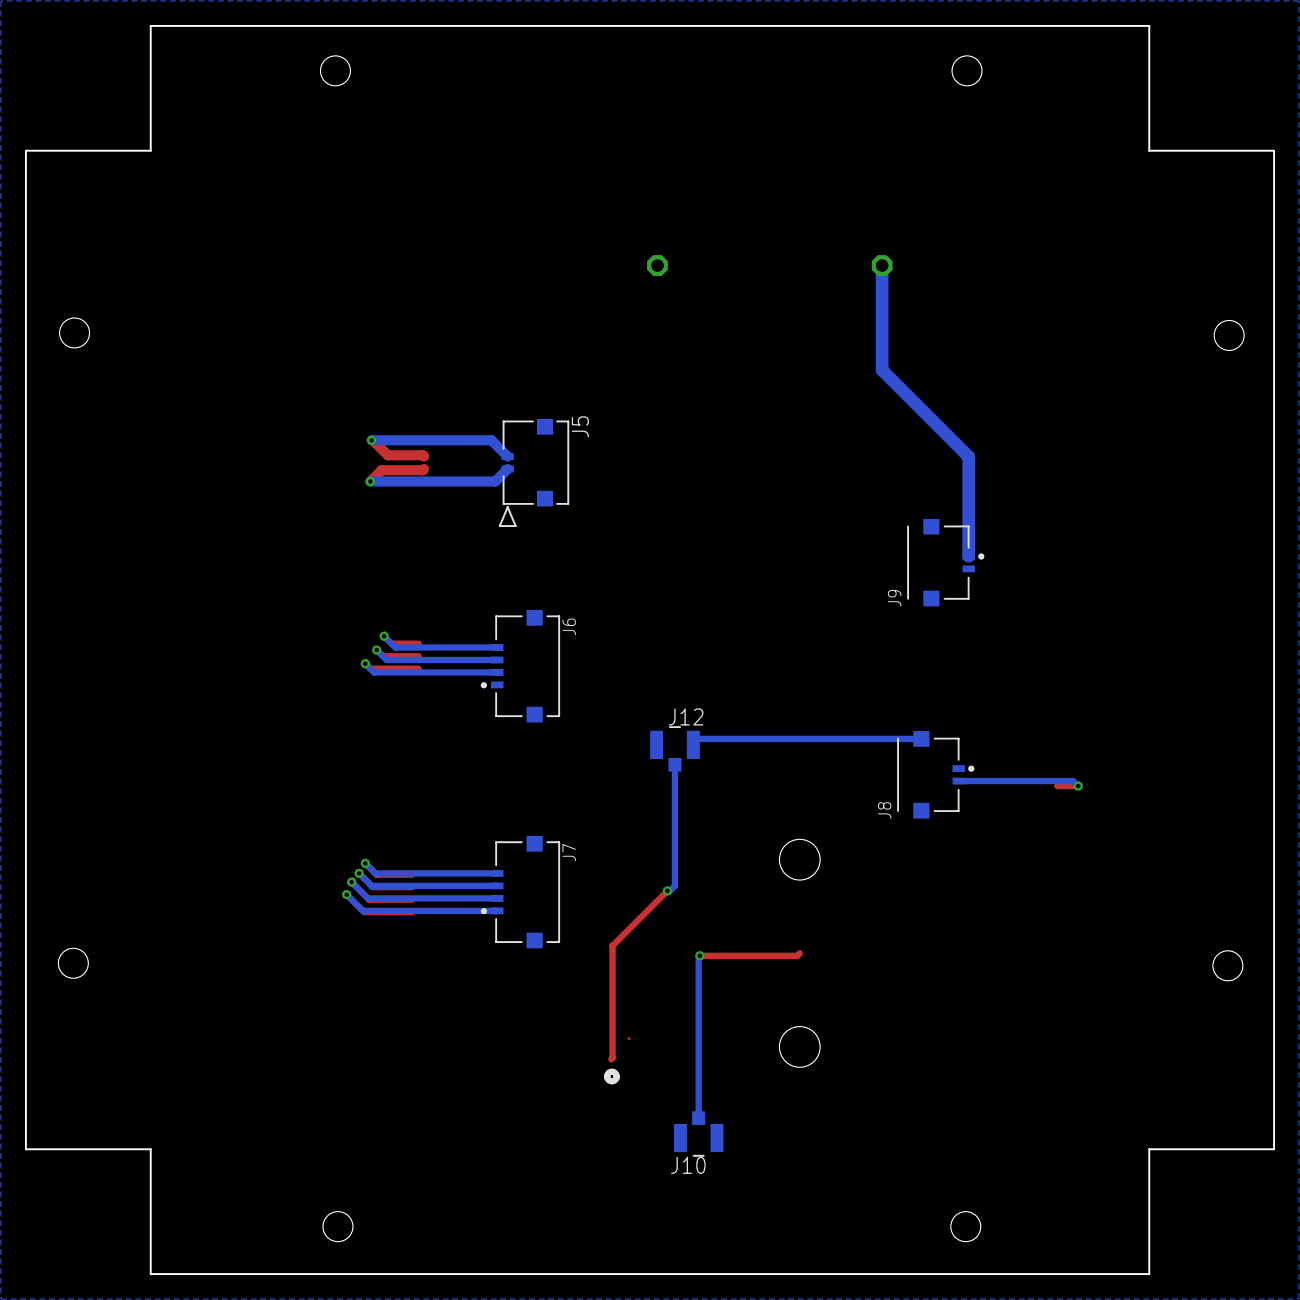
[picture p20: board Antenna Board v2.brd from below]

Board: 2 copper layers, 100.0 x 100.0 mm, 14 parts (7 on the bottom side), 14 nets.

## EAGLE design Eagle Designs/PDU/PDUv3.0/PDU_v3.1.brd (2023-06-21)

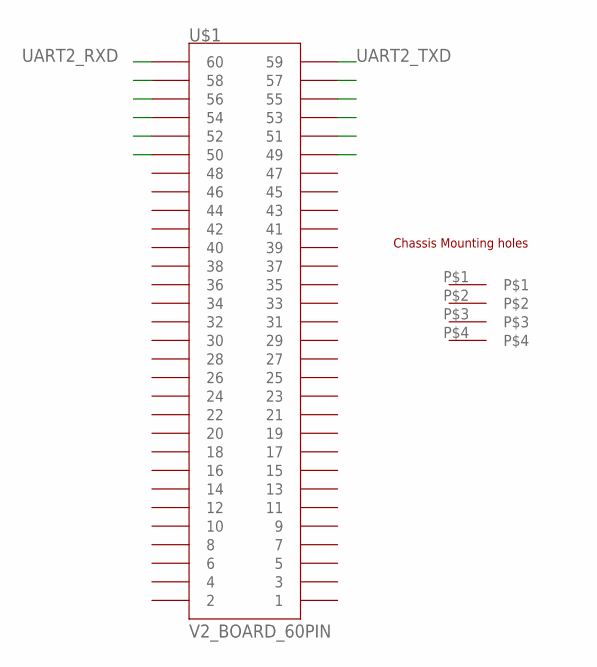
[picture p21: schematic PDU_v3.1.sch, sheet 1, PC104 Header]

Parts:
U$1: V2_BOARD_60PIN; PC104_WCONN_BACKPLANE_HEADER

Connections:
UART2_RXD: U$1.60; also elsewhere on the board
UART2_TXD: U$1.59; also elsewhere on the board

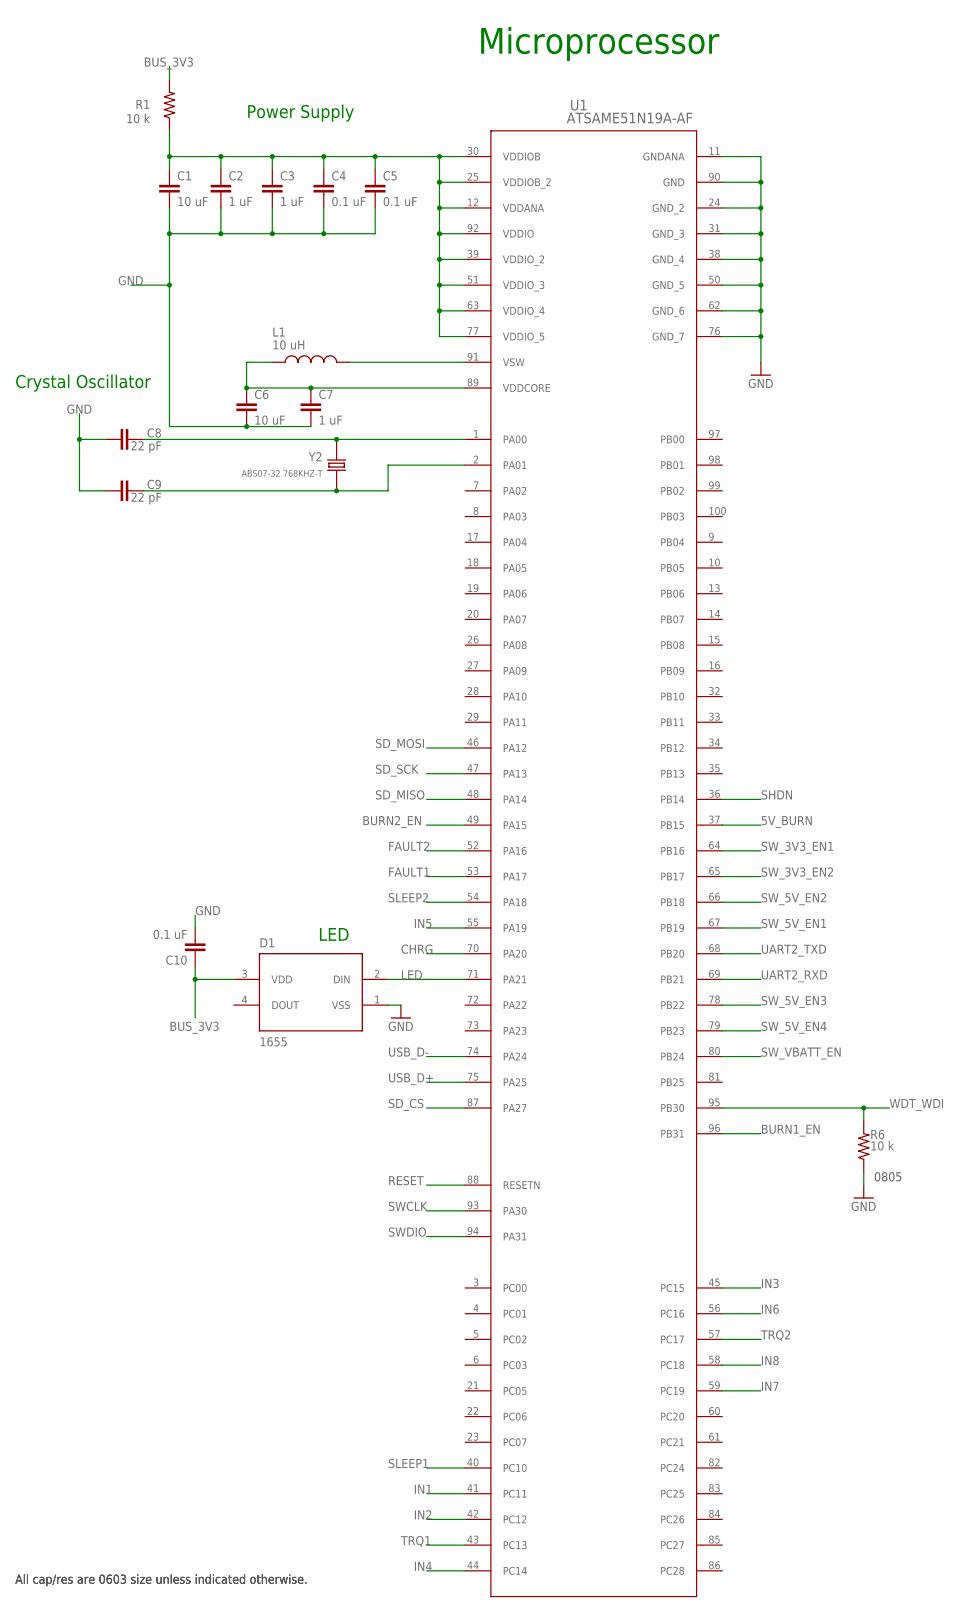
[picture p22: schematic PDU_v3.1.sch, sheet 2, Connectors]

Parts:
C1, C6: 10 uF; 0603-CAP
C2, C3, C7: 1 uF; 0603-CAP
C4, C5, C10: 0.1 uF; 0603-CAP
C8, C9: 22 pF; 0603-CAP
D1: 1655; LED_1655
L1: 10 uH; INDC2012X100N
R1: 10 k; 0603-RES
R6: 10 k; 0805
U1: ATSAME51N19A-AF; TQFP100_14X14MC_MCH
Y2: ABS07-32.768KHZ-T; XTAL_ABS07-32.768KHZ-T

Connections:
5V_BURN: U1.37 (PB15)
BURN1_EN: U1.96 (PB31)
BURN2_EN: U1.49 (PA15)
BUS_3V3: C10.1, D1.3 (VDD), R1.2
CCO_2: C8.2, U1.1 (PA00), Y2.2
CCO_3: C9.2, U1.2 (PA01), Y2.1
CHRG: U1.70 (PA20)
FAULT1: U1.53 (PA17)
FAULT2: U1.52 (PA16)
GND: C1.2, C2.2, C3.2, C4.2, C5.2, C6.2, C7.2, C8.1, C9.1, C10.2, D1.1 (VSS), R6.1, U1.11 (GNDANA), U1.24 (GND_2), U1.31 (GND_3), U1.38 (GND_4), U1.50 (GND_5), U1.62 (GND_6), U1.76 (GND_7), U1.90 (GND); also elsewhere on the board
IN1: U1.41 (PC11)
IN2: U1.42 (PC12)
IN3: U1.45 (PC15)
IN4: U1.44 (PC14)
IN5: U1.55 (PA19)
IN6: U1.56 (PC16)
IN7: U1.59 (PC19)
IN8: U1.58 (PC18)
LED: D1.2 (DIN), U1.71 (PA21)
unnamed: C6.1, C7.1, L1.1, U1.89 (VDDCORE)
unnamed: L1.2, U1.91 (VSW)
RESET: U1.88 (RESETN)
SD_CS: U1.87 (PA27)
SD_MISO: U1.48 (PA14)
SD_MOSI: U1.46 (PA12)
SD_SCK: U1.47 (PA13)
SHDN: U1.36 (PB14)
SLEEP1: U1.40 (PC10)
SLEEP2: U1.54 (PA18)
SWCLK: U1.93 (PA30)
SWDIO: U1.94 (PA31)
SW_3V3_EN1: U1.64 (PB16)
SW_3V3_EN2: U1.65 (PB17)
SW_5V_EN1: U1.67 (PB19)
SW_5V_EN2: U1.66 (PB18)
SW_5V_EN3: U1.78 (PB22)
SW_5V_EN4: U1.79 (PB23)
SW_VBATT_EN: U1.80 (PB24)
TRQ1: U1.43 (PC13)
TRQ2: U1.57 (PC17)
UART2_RXD: U1.69 (PB21); also elsewhere on the board
UART2_TXD: U1.68 (PB20); also elsewhere on the board
USB_D+: U1.75 (PA25)
USB_D-: U1.74 (PA24)
VDD2: C1.1, C2.1, C3.1, C4.1, C5.1, R1.1, U1.12 (VDDANA), U1.25 (VDDIOB_2), U1.30 (VDDIOB), U1.39 (VDDIO_2), U1.51 (VDDIO_3), U1.63 (VDDIO_4), U1.77 (VDDIO_5), U1.92 (VDDIO)
WDT_WDI: R6.2, U1.95 (PB30)

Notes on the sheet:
Microprocessor
LED
Power Supply
Crystal Oscillator
0805
All cap/res are 0603 size unless indicated otherwise.


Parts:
C31, C33: 0.1 uF; 0805
C32: 1 uF; 0805
C34, C100: 4.7 uF; 0805
C35: 10 pF; 0805
C36: 47 uF; 1210
L3: PA4341.222NLT; IND_222NLT_PUL
R22: 18.2 k; 0805
R23: 187 k; 0805
R24: 47 k; 0805
R25, R50: 1 M; 0805
R45: 0; 0805
U22: LT8609A; MSOP-10_MSE

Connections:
BUS_5V: C35.2, C36.1, C100.1, L3.1, R24.2, R25.2
BUS_5V_FB: C35.1, R23.2, R25.1, U22.6 (FB)
BUS_5V_PG: R24.1, U22.8 (PG)
BUS_5V_TRSS: C31.1, U22.7 (TRSS)
BUS_5V_VIN_EN: R45.1, R50.2, U22.10 (EN)
GND: C31.2, C32.2, C34.2, C36.2, C100.2, R22.1, R23.1, R50.1, U22.5 (SYNC), U22.11 (GND); also elsewhere on the board
unnamed: R22.2, U22.4 (RT)
unnamed: C32.1, U22.3 (INTVCC)
unnamed: C33.1, U22.1 (BST)
unnamed: C33.2, L3.2, U22.2 (SW)
VBATT: C34.1, R45.2, U22.9 (VIN)

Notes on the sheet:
Bus is always on
All cap/res are 0805 size unless indicated otherwise.
0 Ohm RES
5V Bus
2.2 uH
1210

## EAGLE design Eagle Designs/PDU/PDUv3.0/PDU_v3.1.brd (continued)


Board: 4 copper layers, 90.2 x 95.5 mm, 32 parts (0 on the bottom side), 21 nets.

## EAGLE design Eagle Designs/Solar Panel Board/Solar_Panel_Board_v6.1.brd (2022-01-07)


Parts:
C1: 0.1uF; 0805
J1, J3: MOLEX_503763-0291MOLEX_503763-0291_0_0; MOLEX_503763-0291_0
J2: MOLEX_503763-0491MOLEX_503763-0491_0_0; MOLEX_503763-0491_0
R1: 45.3k; 0805
R2: 10k; 0805
SC1, SC2, SC3, SC4, SC5, SC6, SC7, SC8, SC9, SC10, SC11, SC12, SC13, SC14, SC15, SC16, SC17, SC18, SC19, SC20, SC21, SC22, SC23, SC24, SC25, SC26, SC27, SC28, SC29, SC30: KXOB25-05X3F
U1: TMP36GSZ; SOIC127P600X175-8N

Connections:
GND: C1.2, J1.3 (MNT_1), J1.4 (MNT_2), J2.3, J2.4, J2.5 (MNT_1), J2.6 (MNT_2), J3.3 (MNT_1), J3.4 (MNT_2), R2.1, SC5.-, SC10.-, SC15.-, SC20.-, SC25.-, SC30.-, U1.4 (GND)
unnamed: J1.1, J1.2
unnamed: SC7.-, SC8.+
unnamed: SC4.-, SC5.+
unnamed: SC3.-, SC4.+
unnamed: SC2.-, SC3.+
unnamed: SC1.-, SC2.+
unnamed: SC8.-, SC9.+
unnamed: SC16.-, SC17.+
unnamed: SC14.-, SC15.+
unnamed: SC13.-, SC14.+
unnamed: SC9.-, SC10.+
unnamed: R1.2, U1.1 (VOUT)
unnamed: SC11.-, SC12.+
unnamed: SC23.-, SC24.+
unnamed: SC22.-, SC23.+
unnamed: SC21.-, SC22.+
unnamed: SC6.-, SC7.+
unnamed: SC17.-, SC18.+
unnamed: SC19.-, SC20.+
unnamed: SC12.-, SC13.+
unnamed: SC28.-, SC29.+
unnamed: SC29.-, SC30.+
unnamed: SC26.-, SC27.+
unnamed: SC24.-, SC25.+
unnamed: SC18.-, SC19.+
unnamed: SC27.-, SC28.+
VCC: J2.1, J2.2, SC1.+, SC6.+, SC11.+, SC16.+, SC21.+, SC26.+
VOUT: J3.2, R1.1, R2.2
VS+: C1.1, J3.1, U1.5 (SHUTDOWN), U1.8 (VS+)



Board: 4 copper layers, 82.4 x 96.7 mm, 37 parts (6 on the bottom side), 30 nets.

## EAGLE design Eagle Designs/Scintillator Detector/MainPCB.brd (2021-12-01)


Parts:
C1: 10uF; 0805
C2, C9: 0.1uF; 0805
C3: 10pF; 0805
C4: 20nF; 0805
C5, C8: 1uF; 0805
C6: 22pF; 0805
C7: 0.47uF; 0805
D1, D2: RBR1VWM40ATR
J1, J2: 503763-0591; CONN_5037630591_MOL
L1: 47uH; IND_LQH32CN470K53L
L2: BK2125LM252-T; BK2125HS_TAY
R1: 1k; 0805
R2: 249; 0805
R3, R4, R10, R13: 10k; 0805
R5, R6: 100k; 0805
R7, R9: 0; 0805
R8: 24.9k; 0805
R11: 226k; 0805
R12: 45.3k; 0805
U1: LT1807IS8PBF; MSOP-8_MS_LIT
U2: LT3461AES6TRMPBF; TSOT-23_S6
U3: TMP36FSZ; SOIC127P600X175-8N
U$1: PC104_WCONN_DETECTOR

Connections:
5V: C1.2, C2.2, C5.2, C9.1, J2.5, L1.2, U1.8 (V+), U2.4 (*SHDN), U2.6 (VIN), U3.5 (SHUTDOWN), U3.8 (VS+)
GND: C1.1, C2.1, C4.2, C5.1, C7.2, C8.2, C9.2, J1.2, J1.4, J1.5, J1.6, J1.7, J2.1, J2.4, J2.6, J2.7, R2.1, R4.2, R5.1, R8.1, R10.1, R13.1, U1.4 (V-), U2.2 (GND), U3.4 (GND)
unnamed: R1.2, U1.3 (+INA)
unnamed: C3.1, R2.2, R3.1, U1.2 (-INA)
unnamed: D2.+, R5.2, R6.1, U1.6 (-INB)
unnamed: C4.1, D1.-, R6.2, R7.1
unnamed: D1.+, D2.-, U1.7 (OUTB)
unnamed: R7.2, R8.2, R9.1
unnamed: L1.1, U2.1 (SW)
unnamed: C6.1, R10.2, R11.1, U2.3 (FB)
unnamed: C6.2, C7.1, L2.2, R11.2, U2.5 (VOUT)
unnamed: R12.2, U3.1 (VOUT)
OUTA: C3.2, R3.2, R4.1, U1.1 (OUTA), U1.5 (+INB)
RASPI_SIG: J2.3, R9.2
SIPM_PWR: C8.1, J1.3, L2.1
SIPM_SIG: J1.1, R1.1
TMP_DATA: J2.2, R12.1, R13.2

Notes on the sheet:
Amplifying circuit
Peak detector
DC-DC boost circuit
Temperature sensor
SiPM connector
Power
Signals going to RasPi



Board: 2 copper layers, 90.2 x 95.5 mm, 32 parts (30 on the bottom side), 17 nets.

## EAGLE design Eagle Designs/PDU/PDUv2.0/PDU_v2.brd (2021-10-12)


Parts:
H1: PC104_WCONN
R72, R73, R74, R75: 1 M; 0603-RES

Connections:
AIN1: H1.1.3; also elsewhere on the board
AIN2: H1.1.4; also elsewhere on the board
AIN3: H1.1.5; also elsewhere on the board
AIN4: H1.1.6; also elsewhere on the board
AIN5: H1.1.7; also elsewhere on the board
AIN6: H1.1.8; also elsewhere on the board
BATT_CHRG: H1.2.41, H1.2.42, H1.2.43, H1.2.44; also elsewhere on the board
BUS_3V3: H1.2.27, H1.2.28; also elsewhere on the board
BUS_5V: H1.2.25, H1.2.26; also elsewhere on the board
CUS_SCL: H1.1.43; also elsewhere on the board
CUS_SDA: H1.1.41; also elsewhere on the board
GND: H1.2.7, H1.2.9, H1.2.14, H1.2.17, H1.2.21, H1.2.22, H1.2.29, H1.2.30, H1.2.32, H1.2.47, H1.2.48, R72.1, R73.1, R74.1, R75.1; also elsewhere on the board
unnamed: H1.P$1, R72.2
unnamed: H1.P$4, R75.2
unnamed: H1.P$2, R73.2
unnamed: H1.P$3, R74.2
RESET: H1.1.52; also elsewhere on the board
SW_3V3_1: H1.2.19; also elsewhere on the board
SW_3V3_2: H1.2.20; also elsewhere on the board
SW_5V_1: H1.2.13; also elsewhere on the board
SW_5V_2: H1.2.15; also elsewhere on the board
SW_5V_3: H1.2.16; also elsewhere on the board
SW_5V_4: H1.2.23; also elsewhere on the board
SW_VBATT: H1.2.45, H1.2.46; also elsewhere on the board
UART2_RXD: H1.1.1; also elsewhere on the board
UART2_TXD: H1.1.2; also elsewhere on the board
VBATT: H1.2.35, H1.2.36; also elsewhere on the board

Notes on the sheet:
PC 104 Header


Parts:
J1, J2, J3, J4, J5, J6, J12, J16, J17, J19, J22, J23, J24, J25: 5037630291; CON_5037630291
J9: 5037630491; CON_5037630491
J11: UJ31-CH-G1-SMT-TR; CUI_UJ31-CH-G1-SMT-TR
J20: 503182-1852; MOLEX_503182-1852
J27: 5037630691; CONN_503763-0691_MOL
R42: 10 k; 0603-RES
R48, R49: 5.1 k; 0603-RES

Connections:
5V_USB_CHRG: J12.1; also elsewhere on the board
AIN2: J19.2; also elsewhere on the board
AIN3: J22.2; also elsewhere on the board
AIN4: J23.2; also elsewhere on the board
AIN5: J24.2; also elsewhere on the board
AIN6: J25.2; also elsewhere on the board
BATT_CHRG: J17.1; also elsewhere on the board
BUS_3V3: J19.1, J20.4 (VDD), J22.1, J23.1, J24.1, J25.1, J27.1, R42.2; also elsewhere on the board
GND: J1.2, J1.3, J1.4, J2.2, J2.3, J2.4, J3.2, J3.3, J3.4, J4.2, J4.3, J4.4, J5.2, J5.3, J5.4, J6.2, J6.3, J6.4, J9.2, J9.4, J9.5, J9.6, J11.A1 (GND), J11.A12 (GND), J11.B1 (GND), J11.B12 (GND), J11.SH1 (SHIELD), J11.SH2 (SHIELD), J11.SH3 (SHIELD), J11.SH4 (SHIELD), J11.SH5 (SHIELD), J11.SH6 (SHIELD), J12.2, J12.3, J12.4, J16.2, J16.3, J16.4, J17.2, J17.3, J17.4, J19.3, J19.4, J20.6 (VSS), J20.P1 (SHIELD), J20.P2 (SHIELD), J20.P3 (SHIELD), J20.P4 (SHIELD), J20.P5 (SHIELD), J22.3, J22.4, J23.3, J23.4, J24.3, J24.4, J25.3, J25.4, J27.2, J27.5, R48.1, R49.1; also elsewhere on the board
RESET: J27.6; also elsewhere on the board
SD_CS: J20.1 (DATA2), R42.1; also elsewhere on the board
SD_MISO: J20.7 (DAT0); also elsewhere on the board
SD_MOSI: J20.3 (CMD); also elsewhere on the board
SD_SCK: J20.5 (CLK); also elsewhere on the board
SOLAR_IN1: J1.1; also elsewhere on the board
SOLAR_IN2: J2.1; also elsewhere on the board
SOLAR_IN3: J3.1; also elsewhere on the board
SOLAR_IN4: J4.1; also elsewhere on the board
SOLAR_IN5: J5.1; also elsewhere on the board
SOLAR_IN6: J6.1; also elsewhere on the board
SWCLK: J27.4; also elsewhere on the board
SWDIO: J27.3; also elsewhere on the board
SW_3V3_1: J9.1; also elsewhere on the board
SW_5V_3: J9.3; also elsewhere on the board
USB_CC1: J11.A5 (CC1), R48.2
USB_CC2: J11.B5 (CC2), R49.2
USB_D+: J11.A6 (DP1), J11.B6 (DP2); also elsewhere on the board
USB_D-: J11.A7 (DN1), J11.B7 (DN2); also elsewhere on the board
VBATT: J16.1; also elsewhere on the board
VBUS: J11.A4 (VBUS), J11.A9 (VBUS), J11.B4 (VBUS), J11.B9 (VBUS)

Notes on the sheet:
USB Charge Connector
Solar Panel Connectors
Breakout Power Connectors
USB Connector
MicroSD Connector
JTAG Connector
SWDIO - JTAG_TMS SWCLK - JTAG_TCK
PyCubed Battery Board Connectors
Samsung 35E 18650 (~ 7.2V Max)
Kapton Heater Tape Connector
Temperature Sensor (Solar Panel Board)
Temperature Sensor (Battery Board)
0603
SW_5V_2 (5V Switch #2) is connected to 68016-202HLF (Connector Header Right Angle) *Added VIA on Board


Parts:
C30: 1 uF; 0805
C37: 0.1 uF; 0805
C61, C65, C67: 4.7 uF; 1206
C66: 22 uF; CAPMP7343X430N
FB3: 330; 0805
R39: 0; RESC5025X70N

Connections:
FB3_L3: C65.1, FB3.2, R39.1
GND: C30.2, C37.2, C61.2, C65.2, C66.2, C67.2; also elsewhere on the board
VBATT: C30.1, C37.1, C61.1, FB3.1; also elsewhere on the board
VBATT_FILT: C66.1, C67.1, R39.2; also elsewhere on the board

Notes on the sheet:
1206
2917
0805
0 Ohm RES
Battery Filtered from 7.2 V (Max) to 6.2 ~ 6.5 V


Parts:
C25, C27: 0.1 uF; 0805
C26, C28: 10 uF; 0805
J7, J8: 5037630491; CON_5037630491
R18, R19, R20, R21: 330 m; 0805
R43, R44: 3.3 k; 0805
U1, U2: DRV8847PWPR; SOP65P640X120-17N

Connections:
BUS_3V3: R43.1, R44.1; also elsewhere on the board
BUS_5V: C25.2, C26.2, C27.2, C28.2, U1.12 (VM), U2.12 (VM); also elsewhere on the board
FAULT1: R43.2, U1.8 (NFAULT); also elsewhere on the board
FAULT2: R44.2, U2.8 (NFAULT)
GND: C25.1, C26.1, C27.1, C28.1, J7.5, J7.6, J8.5, J8.6, R18.1, R19.1, R20.1, R21.1, U1.13 (GND), U2.13 (GND); also elsewhere on the board
IN1: U1.16 (IN1); also elsewhere on the board
IN2: U1.15 (IN2); also elsewhere on the board
IN3: U1.9 (IN3); also elsewhere on the board
IN4: U1.10 (IN4); also elsewhere on the board
IN5: U2.16 (IN1); also elsewhere on the board
IN6: U2.15 (IN2); also elsewhere on the board
IN7: U2.9 (IN3); also elsewhere on the board
IN8: U2.10 (IN4); also elsewhere on the board
unnamed: R19.2, U1.6 (ISEN34)
unnamed: R18.2, U1.3 (ISEN12)
unnamed: R21.2, U2.6 (ISEN34)
unnamed: R20.2, U2.3 (ISEN12)
SLEEP1: U1.1 (NSLEEP); also elsewhere on the board
SLEEP2: U2.1 (NSLEEP); also elsewhere on the board
TORQUE_1A: J7.1, U1.2 (OUT1)
TORQUE_1B: J7.2, U1.4 (OUT2)
TORQUE_2A: J7.4, U1.7 (OUT3)
TORQUE_2B: J7.3, U1.5 (OUT4)
TORQUE_3A: J8.1, U2.2 (OUT1)
TORQUE_3B: J8.2, U2.4 (OUT2)
TORQUE_4A: J8.4, U2.7 (OUT3)
TORQUE_4B: J8.3, U2.5 (OUT4)
TRQ1: U1.11 (TRQ); also elsewhere on the board
TRQ2: U2.11 (TRQ); also elsewhere on the board

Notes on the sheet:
H-Bridge Circuit
All cap/res are 0805 size.


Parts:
C6, C9, C11, C13, C15, C19: 1 uF; 0805
C7: 0.1 uF; 0805
U3, U4, U5, U6, U7, U9: LTC1477CS8LINEAR_TECHNOLOGY_LTC1477CS8_0_2; LINEAR_TECHNOLOGY_LTC1477CS8_2
U16: MIC2514YM5-TR; SOT-23-5_M5_MCH

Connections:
BUS_3V3: U3.2 (VIN1), U3.3 (VINS), U3.7 (VIN2), U9.2 (VIN1), U9.3 (VINS), U9.7 (VIN2); also elsewhere on the board
BUS_5V: U4.2 (VIN1), U4.3 (VINS), U4.7 (VIN2), U5.2 (VIN1), U5.3 (VINS), U5.7 (VIN2), U6.2 (VIN1), U6.3 (VINS), U6.7 (VIN2), U7.2 (VIN1), U7.3 (VINS), U7.7 (VIN2); also elsewhere on the board
GND: C6.2, C7.2, C9.2, C11.2, C13.2, C15.2, C19.2, U3.5 (GND), U4.5 (GND), U5.5 (GND), U6.5 (GND), U7.5 (GND), U9.5 (GND), U16.2 (GND); also elsewhere on the board
SW_3V3_1: C6.1, U3.1 (1_VOUT), U3.8 (2_VOUT); also elsewhere on the board
SW_3V3_2: C19.1, U9.1 (1_VOUT), U9.8 (2_VOUT); also elsewhere on the board
SW_3V3_EN1: U3.4 (EN); also elsewhere on the board
SW_3V3_EN2: U9.4 (EN); also elsewhere on the board
SW_5V_1: C11.1, U5.1 (1_VOUT), U5.8 (2_VOUT); also elsewhere on the board
SW_5V_2: C13.1, U6.1 (1_VOUT), U6.8 (2_VOUT); also elsewhere on the board
SW_5V_3: C15.1, U7.1 (1_VOUT), U7.8 (2_VOUT); also elsewhere on the board
SW_5V_4: C9.1, U4.1 (1_VOUT), U4.8 (2_VOUT); also elsewhere on the board
SW_5V_EN1: U5.4 (EN); also elsewhere on the board
SW_5V_EN2: U6.4 (EN); also elsewhere on the board
SW_5V_EN3: U7.4 (EN); also elsewhere on the board
SW_5V_EN4: U4.4 (EN); also elsewhere on the board
SW_VBATT: U16.4 (OUT); also elsewhere on the board
SW_VBATT_EN: U16.1 (CTL); also elsewhere on the board
VBATT_FILT: C7.1, U16.3 (IN); also elsewhere on the board

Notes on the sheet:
3V3 Switches
5V Switches
Breakout Power
BBB
Kapton Heater
All cap are 0805 size.
12V Switch Regulator
VBATT Switch

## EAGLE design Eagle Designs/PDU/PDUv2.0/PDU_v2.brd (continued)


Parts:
C1, C2: 22 uF; 0805
C3, C16, C45, C51, C87: 0.1 uF; 0805
C4, C17: 1 uF; 0805
C43, C47, C48, C86, C88: 4.7 uF; 0805
C44: 1uF; 0805
C46, C49: 10 uF; 0805
C50: 0.47 uF; 0805
C52: 100 pF; 0805
C53: 4.7 nF; 0805
C74, C75, C76, C77, C78, C79, C80, C81: 33 uF; 1206
C84: 10 pF; 0805
C85: 47 uF; 1210
D4: DIODE_SOD-123FL; SOD-123FL
J10: 5037630491; CON_5037630491
L5: 6 uH; 7443551600
L6: PA4341.222NLT; IND_222NLT_PUL
M1, M2: BSZ100N06LS3
M3, M4: BSZ033NE2LS5; BSZ100N06LS3
R1: 4 m; 0805
R2: 390 k; 0805
R3: 180 k; 0805
R4: 15 m; 0805
R5: 130 k; 0805
R6, R33, R69: 100 k; 0805
R30, R32: 10 k; 0805
R31: 27 k; 0805
R46: 510 k; 0805
R47: 270 k; 0805
R68: 40.2 k; 0805
R70: 1 M; 0805
R71: 69.8 k; 0805
U8: LT8609A; MSOP-10_MSE
U13: LT8390EFE#PBF; SOP65P640X120-29N

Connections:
12V_OUT: C78.1, C79.1, C80.1, C81.1, C88.1, D4.A, D4.C, R4.2, R5.2, R46.1, U8.9 (VIN), U13.15 (ISN)
12V_SW1: C84.2, C85.1, C86.1, J10.1, J10.2, L6.1, R69.2, R70.2
BST_3V3_BUS: C87.1, U8.1 (BST)
FB_3V3_BUS: C84.1, R70.1, R71.2, U8.6 (FB)
GND: C1.2, C2.2, C4.2, C16.2, C17.2, C43.2, C44.2, C46.2, C47.2, C48.2, C49.2, C50.2, C51.2, C52.2, C53.2, C74.2, C75.2, C76.2, C77.2, C78.2, C79.2, C80.2, C81.2, C85.2, C86.2, C88.2, J10.3, J10.4, J10.5, J10.6, M2.P$2 (S), M2.P$3 (S), M2.P$4 (S), M3.P$2 (S), M3.P$3 (S), M3.P$4 (S), R3.1, R30.1, R33.1, R47.1, R68.1, R71.1, U8.5 (SYNC), U8.11 (GND), U13.10 (TEST), U13.22 (SYNC/SPRD), U13.29 (GND); also elsewhere on the board
unnamed: C3.1, M1.P$2 (S), M1.P$3 (S), M1.P$4 (S), M2.P$5 (D), M2.P$6 (D), M2.P$7 (D), M2.P$8 (D), M2.P$9 (D), R1.2, U13.3 (SW1), U13.5 (LSP)
unnamed: C3.2, U13.2 (BST1)
unnamed: M2.P$1 (G), U13.1 (BG1)
unnamed: M1.P$1 (G), U13.4 (TG1)
unnamed: M3.P$1 (G), U13.28 (BG2)
unnamed: C52.1, R31.2, U13.20 (VC)
unnamed: R5.1, R32.2
unnamed: C45.1, L5.P$2, M3.P$5 (D), M3.P$6 (D), M3.P$7 (D), M3.P$8 (D), M3.P$9 (D), M4.P$2 (S), M4.P$3 (S), M4.P$4 (S), U13.26 (SW2)
unnamed: C43.1, R6.2, U13.8 (INTVCC)
unnamed: L5.P$1, R1.1, U13.6 (LSN)
unnamed: C45.2, U13.27 (BST2)
unnamed: C44.1, C46.1, C49.1, C74.1, C75.1, C76.1, C77.1, M4.P$5 (D), M4.P$6 (D), M4.P$7 (D), M4.P$8 (D), M4.P$9 (D), R4.1, U13.14 (ISP), U13.24 (VOUT)
unnamed: M4.P$1 (G), U13.25 (TG2)
unnamed: C51.1, U13.18 (SS)
unnamed: R33.2, U13.21 (RT)
unnamed: C53.1, R31.1
PG_3V3_BUS: R69.1, U8.8 (PG)
RT_3V3_BUS: R68.2, U8.4 (RT)
SW_3V3_BUS: C87.2, L6.2, U8.2 (SW)
SW_5V_4: C1.1, C2.1, C4.1, C47.1, C48.1, M1.P$5 (D), M1.P$6 (D), M1.P$7 (D), M1.P$8 (D), M1.P$9 (D), R2.2, U13.7 (VIN); also elsewhere on the board
SW_12V_EN1: R2.1, R3.2, U8.10 (EN), U13.9 (EN/UVLO); also elsewhere on the board
SW_12V_FB: R30.2, R32.1, U13.19 (FB)
SW_12V_IN1: C50.1, U13.11 (LOADEN), U13.12 (VREF), U13.13 (CTRL)
SW_12V_PGOOD: R6.1, U13.17 (!PGOOD)
TRSS_3V3_BUS: C16.1, U8.7 (TRSS)
VCC_3V3_BUS: C17.1, U8.3 (INTVCC)
V_BATT_SENSE: R46.2, R47.2

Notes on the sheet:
Vin Shutoff @ 6.3v
12V Switch Regulator
6 uH
1206
2.2 uH
1210
All cap/res are 0805 size unless indicated otherwise.
*15V converts to 12V
*5V converts to 15V


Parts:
C5, C21, C31, C33: 0.1 uF; 0805
C20, C32: 1 uF; 0805
C22, C34, C99, C100: 4.7 uF; 0805
C23, C35: 10 pF; 0805
C24, C36: 47 uF; 1210
L1, L3: PA4341.222NLT; IND_222NLT_PUL
R14, R22: 18.2 k; 0805
R15: 301 k; 0805
R16, R24: 47 k; 0805
R17, R25, R41, R50: 1 M; 0805
R23: 180 k; 0805
R40, R45: 0; 0805
U21, U22: LT8609A; MSOP-10_MSE

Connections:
BUS_3V3: C23.2, C24.1, C99.1, L1.1, R16.2, R17.2; also elsewhere on the board
BUS_3V3_FB: C23.1, R15.2, R17.1, U21.6 (FB)
BUS_3V3_PG: R16.1, U21.8 (PG)
BUS_3V3_TRSS: C5.1, U21.7 (TRSS)
BUS_3V3_VIN_EN: R40.1, R41.2, U21.10 (EN)
BUS_5V: C35.2, C36.1, C100.1, L3.1, R24.2, R25.2; also elsewhere on the board
BUS_5V_FB: C35.1, R23.2, R25.1, U22.6 (FB)
BUS_5V_PG: R24.1, U22.8 (PG)
BUS_5V_TRSS: C31.1, U22.7 (TRSS)
BUS_5V_VIN_EN: R45.1, R50.2, U22.10 (EN)
GND: C5.2, C20.2, C22.2, C24.2, C31.2, C32.2, C34.2, C36.2, C99.2, C100.2, R14.1, R15.1, R22.1, R23.1, R41.1, R50.1, U21.5 (SYNC), U21.11 (GND), U22.5 (SYNC), U22.11 (GND); also elsewhere on the board
unnamed: C20.1, U21.3 (INTVCC)
unnamed: R14.2, U21.4 (RT)
unnamed: C21.1, U21.1 (BST)
unnamed: C21.2, L1.2, U21.2 (SW)
unnamed: R22.2, U22.4 (RT)
unnamed: C32.1, U22.3 (INTVCC)
unnamed: C33.1, U22.1 (BST)
unnamed: C33.2, L3.2, U22.2 (SW)
VBATT_FILT: C22.1, C34.1, R40.2, R45.2, U21.9 (VIN), U22.9 (VIN); also elsewhere on the board

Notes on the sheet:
0 Ohm RES
Bus is always on
3V3 Bus
5V Bus
2.2 uH
1210
All cap/res are 0805 size unless indicated otherwise.


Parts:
J13, J14: 5037630291; CON_5037630291
R7, R10, R13, R86: 10 k; 0603-RES
R8, R11: 100 k; 0603-RES
R9, R12: 4.7 k; 0603-RES
U11, U12: IRLML2803PBFCT-ND; PG-TO23-3_INF
U23: BC848ALT1G; SOT-23_ONS
U25: SI4835DDY-T1-GE3; SOIC_DY-T1-GE3_VIS
U26, U27: SI3493DDV-T1-GE3; 6TSOP_VIS

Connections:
5V_BURN: R7.2, U23.1 (BASE); also elsewhere on the board
BURN1_EN: R9.2, R10.1; also elsewhere on the board
BURN2_EN: R12.2, R13.1; also elsewhere on the board
GND: J13.1, J13.3, J13.4, J14.1, J14.3, J14.4, R7.1, R10.2, R13.2, U11.2 (S), U12.2 (S), U23.2 (EMITTER); also elsewhere on the board
unnamed: R8.2, R11.2, U25.5 (D1), U25.6 (D2), U25.7 (D3), U25.8 (D4), U26.4 (S), U27.4 (S)
unnamed: R12.1, U12.1 (G)
unnamed: R11.1, U12.3 (D), U27.3 (G)
unnamed: R86.1, U23.3 (COLLECTOR), U25.4 (G)
unnamed: R9.1, U11.1 (G)
unnamed: R8.1, U11.3 (D), U26.3 (G)
VBATT: R86.2, U25.1 (S1), U25.2 (S2), U25.3 (S3); also elsewhere on the board
VBURN1: J13.2, U26.1 (D_2), U26.2 (D_3), U26.5 (D_4), U26.6 (D)
VBURN2: J14.2, U27.1 (D_2), U27.2 (D_3), U27.5 (D_4), U27.6 (D)

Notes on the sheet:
Burn Wire Circuit
All resistors in 0603 size.

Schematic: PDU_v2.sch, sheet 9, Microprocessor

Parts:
C54, C56: 10 uF; 0603-CAP
C55, C57, C58: 1 uF; 0603-CAP
C59, C60, C64: 0.1 uF; 0603-CAP
C62, C63: 22 pF; 0603-CAP
C72: 0.1 uF; 0805
C73: 1 uF; 0805
D2: 1655; LED_1655
L4: 10 uH; INDC2012X100N
R38: 10 k; 0603-RES
R51, R57: 10 k; 0805
R58: 2 k; 0805
R59: 100 k; 0805
R60: 63.4 k; 0805
U14: ATSAME51N19A-AF; TQFP100_14X14MC_MCH
U17: MAX16998AAUA+T; 21-0036K_MXM
Y1: ABS07-32.768KHZ-T; XTAL_ABS07-32.768KHZ-T

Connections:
5V_BURN: U14.37 (PB15); also elsewhere on the board
BURN1_EN: U14.96 (PB31); also elsewhere on the board
BURN2_EN: U14.49 (PA15); also elsewhere on the board
BUS_3V3: C64.1, D2.3 (VDD), R38.2, R58.2, R60.2; also elsewhere on the board
CCO_0: C62.2, U14.1 (PA00), Y1.2
CCO_1: C63.2, U14.2 (PA01), Y1.1
CUS_SCL: U14.35 (PB13); also elsewhere on the board
CUS_SDA: U14.34 (PB12); also elsewhere on the board
FAULT1: U14.53 (PA17); also elsewhere on the board
GND: C54.2, C55.2, C56.2, C57.2, C58.2, C59.2, C60.2, C62.1, C63.1, C64.2, C72.1, C73.2, D2.1 (VSS), R51.1, R59.1, U14.11 (GNDANA), U14.24 (GND_2), U14.31 (GND_3), U14.38 (GND_4), U14.50 (GND_5), U14.62 (GND_6), U14.76 (GND_7), U14.90 (GND), U17.5 (GND); also elsewhere on the board
IN1: U14.41 (PC11); also elsewhere on the board
IN2: U14.42 (PC12); also elsewhere on the board
IN3: U14.45 (PC15); also elsewhere on the board
IN4: U14.44 (PC14); also elsewhere on the board
IN5: U14.55 (PA19); also elsewhere on the board
IN6: U14.56 (PC16); also elsewhere on the board
IN7: U14.59 (PC19); also elsewhere on the board
IN8: U14.58 (PC18); also elsewhere on the board
LED: D2.2 (DIN), U14.71 (PA21)
unnamed: L4.2, U14.91 (VSW)
unnamed: C54.1, C55.1, L4.1, U14.89 (VDDCORE)
unnamed: C72.2, U17.3 (SRT)
unnamed: C73.1, U17.4 (SWT)
unnamed: R59.2, R60.1, U17.2 (RESETIN)
RESET: R58.1, U14.88 (RESETN), U17.7 (!RESET); also elsewhere on the board
SD_CS: U14.87 (PA27); also elsewhere on the board
SD_MISO: U14.48 (PA14); also elsewhere on the board
SD_MOSI: U14.46 (PA12); also elsewhere on the board
SD_SCK: U14.47 (PA13); also elsewhere on the board
SLEEP1: U14.40 (PC10); also elsewhere on the board
SLEEP2: U14.54 (PA18); also elsewhere on the board
SWCLK: U14.93 (PA30); also elsewhere on the board
SWDIO: U14.94 (PA31); also elsewhere on the board
SW_3V3_EN1: U14.64 (PB16); also elsewhere on the board
SW_3V3_EN2: U14.65 (PB17); also elsewhere on the board
SW_5V_EN1: U14.67 (PB19); also elsewhere on the board
SW_5V_EN2: U14.66 (PB18); also elsewhere on the board
SW_5V_EN3: U14.78 (PB22); also elsewhere on the board
SW_5V_EN4: U14.79 (PB23); also elsewhere on the board
SW_12V_EN1: U14.61 (PC21); also elsewhere on the board
SW_VBATT_EN: U14.80 (PB24); also elsewhere on the board
TRQ1: U14.43 (PC13); also elsewhere on the board
TRQ2: U14.57 (PC17); also elsewhere on the board
UART2_RXD: U14.69 (PB21); also elsewhere on the board
UART2_TXD: U14.68 (PB20); also elsewhere on the board
USB_D+: U14.75 (PA25); also elsewhere on the board
USB_D-: U14.74 (PA24); also elsewhere on the board
VBATT_FILT: R57.2, U17.1 (IN); also elsewhere on the board
VDD: C56.1, C57.1, C58.1, C59.1, C60.1, R38.1, U14.12 (VDDANA), U14.25 (VDDIOB_2), U14.30 (VDDIOB), U14.39 (VDDIO_2), U14.51 (VDDIO_3), U14.63 (VDDIO_4), U14.77 (VDDIO_5), U14.92 (VDDIO)
WDT_EN: R57.1, U17.8 (!ENABLE)
WDT_WDI: R51.2, U14.95 (PB30), U17.6 (WDI)

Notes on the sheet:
Microprocessor
LED
Watchdog Timer
Power Supply
Crystal Oscillator
0805
All cap/res are 0603 size unless indicated otherwise.
All cap/res in WDT circuit are 0805 size.

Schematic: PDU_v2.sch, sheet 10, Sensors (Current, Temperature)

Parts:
C29: 0.1 uF; 0805
C82: 0.1 uF; 0603-CAP
R34, R36: 3.3 k; 0805
R35: 2 m; 0805
R61: 27 k; 0603-RES
R62: 10 k; 0603-RES
U15: INA219BIDR; SOIC127P599X175-8N
U18: TMP36FSZ; R_8_ADI
U$2, U$4: TEST_POINT

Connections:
A0: U15.2 (A0), U$2.1
A1: U15.1 (A1), U$4.1
AIN1: R61.1, R62.2; also elsewhere on the board
BUS_3V3: C29.1, C82.2, R34.1, R36.1, U15.5 (VS), U18.5 (!SHUTDOWN), U18.8 (+VS); also elsewhere on the board
CUS_SCL: R36.2, U15.4 (SCL); also elsewhere on the board
CUS_SDA: R34.2, U15.3 (SDA); also elsewhere on the board
GND: C29.2, C82.1, R62.1, U15.6 (GND), U18.4 (GND); also elsewhere on the board
unnamed: R35.2, U15.7 (VIN-)
unnamed: R61.2, U18.1 (VOUT)
SOLAR_IN1: R35.1, U15.8 (VIN+); also elsewhere on the board

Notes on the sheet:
All cap/res in current sensor circuit is 0805 size.
All cap/res in temp sensor is 0603 size.
Current Sensor
Analog Temperature Sensor
CUS_SCL, CUS_SDA - I2C

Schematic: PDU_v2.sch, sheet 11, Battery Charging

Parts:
C38, C41, C93: 1 uF; 0603-CAP
C39: 33 pF; 0603-CAP
C40, C91: 0.1 uF; 0603-CAP
C42, C90: 4.7 uF; 0603-CAP
C89, C92: 10 uF; 0603-CAP
CR1, CR2, CR3, CR4, CR5, CR6, CR7: PMEG10020ELRX; CFP3_SOD123W_NEX
D3: SBR2A40P1Q-7; POWERDI-123
J18: 5037630491; CON_5037630491
L7: PA4341.222NLT; IND_222NLT_PUL
LED2, LED3: LED_0805
NT1, NT2, NT3: AIMC-0805-2N2S-T; INDC2012X105N
R26, R80, R81: 1 k; 0603-RES
R27: 100; 0603-RES
R28, R77: 10 k; 0603-RES
R29: 40.2 k; 0603-RES
R37, R78: 2 k; 0603-RES
R76: 27.4 k; 0603-RES
R79: 68.1 k; 0603-RES
R84: 10 k; 0805
R85: 15 k; 0805
R87: 1 M; 0603-RES
R88: 150 k; 0603-RES
U20: AO3404A; SOT-23-3L_AOS
U$1: MP2639A; QFN26-4X4_MP2639A

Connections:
5V_USB_CHRG: CR7.2 (12); also elsewhere on the board
ACOK: LED2.2, U$1.25 (ACOK_N)
BATT_CHRG: C92.2, C93.2, U$1.3 (VH); also elsewhere on the board
BC_VCC: C41.1, R37.1, R78.2, U$1.9 (VCC)
BST: C91.2, U$1.6 (BST)
CHGOK: LED3.2, U$1.26 (CHGOK)
FB: R80.1, R81.1, U$1.17 (FB)
GND: C42.1, C89.1, C90.1, C92.1, C93.1, D3.A, J18.2, J18.4, J18.5, J18.6, NT1.1, NT2.1, NT3.1, R26.1, U20.1 (G), U$1.5 (PGND), U$1.22 (OLIM); also elsewhere on the board
GNDA: C38.1, C39.1, C40.2, C41.2, NT1.2, NT2.2, R29.1, R77.2, R79.2, R80.2, R88.2, U$1.8 (MODE), U$1.10 (AGND), U$1.13 (LED1), U$1.14 (LED2), U$1.15 (LED3), U$1.16 (LED4)
IB: R28.2, R29.2, U$1.21 (IB)
ILIM: R79.1, U$1.24 (ILIM)
INH_SW1_COM: CR1.1 (11), CR2.1 (11), CR3.1 (11), CR4.1 (11), CR5.1 (11), CR6.1 (11), CR7.1 (11), J18.1
INH_SW1_NC: C42.2, C89.2, C90.2, J18.3, R76.1, U$1.1 (VL)
LX: D3.C, L7.1, U$1.2 (LX)
MID: NT3.2, R27.1, U20.2 (S), U$1.12 (MID)
unnamed: R87.1, U$1.23 (ISET)
unnamed: R87.2, R88.1
unnamed: LED2.1, R78.1
unnamed: LED3.1, R37.2
NTC: R84.1, R85.2, U$1.20 (NTC)
R26_R27: R26.2, R27.2, U20.3 (D)
R28_C39: C39.2, R28.1
R85_C38: C38.2, R85.1
SOLAR_IN1: CR1.2 (12); also elsewhere on the board
SOLAR_IN2: CR2.2 (12); also elsewhere on the board
SOLAR_IN3: CR3.2 (12); also elsewhere on the board
SOLAR_IN4: CR4.2 (12); also elsewhere on the board
SOLAR_IN5: CR5.2 (12); also elsewhere on the board
SOLAR_IN6: CR6.2 (12); also elsewhere on the board
SW: C91.1, L7.2, U$1.4 (SW)
TMR: C40.1, U$1.11 (TMR)
VBATT: R81.2; also elsewhere on the board
VLIM: R76.2, R77.1, U$1.18 (VLIM)
VNTC: R84.2, U$1.19 (VNTC)

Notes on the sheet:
Net Tie
0 F CAP
2.2 uH
0805
All cap/res are 0603 size unless indicated otherwise.
Battery/Solar Charging Region
Solar Cell Inhibit Switch Connectors
(From) Solar Panel Connectors

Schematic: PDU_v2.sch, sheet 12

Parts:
J15: 5037630291; CON_5037630291
R82, R83: 1 M; 0805
U10, U24: AO3404A; SOT-23-3L_AOS

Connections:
GND: J15.3, J15.4, R83.2, U10.2 (S), U24.2 (S); also elsewhere on the board
unnamed: R82.1, U10.3 (D), U24.1 (G)
RBF_OUT: J15.2, R83.1, U10.1 (G)
VBATT: J15.1, R82.2, U24.3 (D); also elsewhere on the board

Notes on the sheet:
0805
Pin Removed = Open Circuit = PDU v2 Powered On Pin In = Closed Circuit = PDU v2 Powered Off
Remove Before Flight (RBF) Circuit



Board: 4 copper layers, 90.2 x 95.5 mm, 245 parts (108 on the bottom side), 178 nets.

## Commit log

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2021-02-19 organizing the hardware folder, adding an Eagle folder for our designs
    [On Board Computer.brd, On Board Computer.sch, Solar Panel Board.brd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]
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2021-02-19 Surface mount connectors connected to ground
    [Solar Panel Board.brd, Solar Panel Board.sch]
2021-02-19 Moved solar panel boards to Eagle folder, deleted redudant OBC files
    [On Board Computer.brd, On Board Computer.sch, Solar Panel Board.brd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]
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2021-03-01 Added payload board Eagle files
    [Payload.brd, Payload.sch, Solar Panel Board BOM.xlsx]
2021-03-06 Edited payload board, created payload and bbb obc BOM
    [On Board Computer.brd, On Board Computer.csv, On Board Computer.sch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]
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2021-03-09 Update Payload board file
    [Payload.brd]
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2021-03-09 Updated solar panel boards
    [Solar Panel Board.brd, Solar Panel Board.sch]
2021-03-10 Solar panel board changes
    Added temp sensor and external connector to solar panel board; updated solar panel board BOM
    [Solar Panel Board BOM.xlsx, Solar Panel Board.brd, Solar Panel Board.csv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]
2021-03-19 Added antenna board Eagle files and BOM
    [Antenna Board.brd, Antenna Board.csv, Antenna Board.sch]
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2021-05-06 Uploaded Solar Panel Board v2
    [Solar Panel Board v2.brd, Solar Panel Board v2.sch]
2021-05-06 Added values to resistors and capacitors
    Payload - added 3.3k value to pullup resistors for H-bridges
    Solar Panel Board - added 0.1uF value to capacitor for temp sensor
    [Payload.brd, Payload.sch, Solar Panel Board.brd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]
2021-05-06 Updated BOMs and edited Solar Panel Board v2
    [Antenna Board BOM.csv, Antenna Board BOM.xlsx, On Board Computer BOM.csv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]
2021-05-07 Add files via upload
    Edited Solar Panel Board v2
    [Solar Panel Board v2.brd, Solar Panel Board v2.sch]
2021-05-29 Uploaded H-bridge library and design block files
    [HBridge.sch]
2021-05-29 added PDU v2 Eagle files and Artemis Library
    [PDU_v2.brd, PDU_v2.sch]
2021-06-01 updated PDU v2 Eagle files and Artemis Library
    [PDU_v2.brd, PDU_v2.sch]
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2021-07-27 Changed connectors for RBF pin and moved in connectors that interfered with structure.
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2021-08-13 made minor changes to the OBC and BB
    [BOM (OBC v3).csv, BOM (OBC v3).xlsx, BOM batteryboard.csv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]
2021-09-02 fixed naming issues
    [BOM (OBC v3).csv, BOM (OBC v3).xlsx, BOM batteryboard.csv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]
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2021-09-09 made improvements to the solar panel board and included cam outputs
    [Solar Panel Board v3 BOM.csv, Solar_Panel_Board_v5_1.brd, Solar_Panel_Board_v5_1.csv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]
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2021-10-06 uploaded Camera Mount Board schem and board; removed PDU v2 screw terminal
    [PDU_v2.brd, PDU_v2.sch, camera-panel.brd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]
2021-10-12 replaced PDU v2 terminal with Conn Header 0.1'
    [PDU_v2.brd, PDU_v2.sch]
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2021-10-14 added HSFL stencil logo to Camera Mount Panel Board
    [camera-panel.brd]
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2021-11-09 Added antenna board v3, removed extra antenna board v2 files
    [Antenna Board v3.brd, Antenna Board v3.sch, Antenna Board v3.xlsx]
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2021-11-18 Added text to bottom and top of board to denote connectors + temp sensor/torque coils
    [Solar_Panel_Board_v6.1.brd]
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2021-12-01 Edited detector pcb and created battery charging circuit board
    [Battery Charging Circuit.brd, Battery Charging Circuit.sch, Battery Charging Circuit.xlsx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]
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2021-12-08 updated OBC v4.1; verified & updated Battery Charging Circuit
    [OBCv4.1.brd, OBCv4.1.sch, OBCv4.brd]
2021-12-08 Finalized PDU Battery Charging Circuit Design And Added Gerber Files
    [Battery Charging Circuit.brd, OBCv4.1.brd, OBCv4.1.sch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]
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2021-12-22 Completed OBC v4.1 (Finished); Updated PDU v2.1 (Unfinished)
    [OBCv4.1.brd, OBCv4.1.sch, OBCv4.brd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]
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2022-01-07 Made edits to solar panel, antenna, battery boards
    [Antenna Board v4.2.brd, Antenna Board v4.2.sch, Solar_Panel_Board_v6.1.brd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]
2022-01-19 completed PDU v2.1 revisions 01/18/2022 and did minor changes to OBC v4.1
    [Battery Charging Circuit.brd, Battery Charging Circuit.sch, Battery Charging Circuit.xlsx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]
2022-01-20 did OBC v4.1 revisions (replaced Antenna connector); uploaded OBC Eagle Library
    [OBCv4.1.brd, OBCv4.1.sch]
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2022-02-18 revised and finalized OBC v4.20, added OBC v4.20 BOM and Gerber Files
    [OBCv4.20.brd, OBCv4.20.csv, OBCv4.20.sch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]
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2022-03-15 added Kapton Heater Connector (device) to PDU v2.1
    [OBCv4.1.csv, OBCv4.20.brd, PDU_v2.1.brd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]
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2022-04-08 Updated OBC v4.21 with 2 Radios, Added SPI to PC 104 Header, Uploaded Radio Devices Eagle Library
    [OBCv4.1.csv, OBCv4.20.brd, OBCv4.20.csv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]
2022-04-08 Corrected SPI Connections to PC 104 Header
2022-04-14 fixed OBC modular radio Radio Reset connection
    [OBCv4.21.brd, OBCv4.21.sch]
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2022-07-27 created OBC v4.22 and uploaded revised Teensy Library
    [OBCv4.22.brd, OBCv4.22.sch]
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2022-09-23 Removed unnecessary v2 backup Eagle files; added newest OBC revision
    [OBCv4.23.brd, OBCv4.23.sch]
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2022-12-02 cleaned up a wire stub on OBC 4.24 and copied OBC for RF with ground plane
    [OBCv4.24.brd, OBCv4.24.sch]
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2022-12-03 changed radio power supply from 5V_bus to SW_3V3_2 on both the OBCv2.24 and OBCv2.24_RFplane. Added ground station board.
    [OBCv4.24.brd, OBCv4.24.sch, ground_station_boardv1.1.brd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]
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2022-12-09 Updated Artemis v2 EAGLE library, solar panel board, and antenna board
    [Antenna Board v5.0.brd, Antenna Board v5.0.sch, Solar Panel Board v7.0.brd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]
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2023-02-16 Swapped the antenna pad for the MCX connector on the ground station board. Created the mock transmission board which is a radio, teensy and antenna.
    [ground_station_boardv1.1.brd, ground_station_boardv1.1.sch]
2023-02-17 Added RF ground plane to ground station board.
    [ground_station_boardv1.1.brd, ground_station_boardv1.1.sch]
2023-02-28 Modified pin configuration on the ground station board to match OBC 4.24.
    [ground_station_boardv1.1.brd, ground_station_boardv1.1.sch]
2023-03-01 fixed OBC, PDU for Manufacturing Order
    [DRILEGEND.CFG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]
2023-03-14 fixed PDU for manufacturing
    [PDU_v2.2.brd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]
2023-03-23 Fixed RF ground station board... again.
    [ground_station_boardv1.1.brd, ground_station_boardv1.1.sch]
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

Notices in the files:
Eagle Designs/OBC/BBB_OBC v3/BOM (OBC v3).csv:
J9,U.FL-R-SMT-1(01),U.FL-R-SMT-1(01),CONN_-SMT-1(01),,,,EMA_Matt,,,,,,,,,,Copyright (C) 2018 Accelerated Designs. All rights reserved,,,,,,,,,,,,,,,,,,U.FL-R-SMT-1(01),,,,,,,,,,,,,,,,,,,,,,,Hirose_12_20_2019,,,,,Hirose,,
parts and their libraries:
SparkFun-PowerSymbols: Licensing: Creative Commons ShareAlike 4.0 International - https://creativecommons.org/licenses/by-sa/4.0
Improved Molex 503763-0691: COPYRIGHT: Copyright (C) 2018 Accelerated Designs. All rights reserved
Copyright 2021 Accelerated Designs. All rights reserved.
